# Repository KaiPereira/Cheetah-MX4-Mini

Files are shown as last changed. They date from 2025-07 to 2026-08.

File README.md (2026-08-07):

# Cheetah MX4 Mini Motherboard

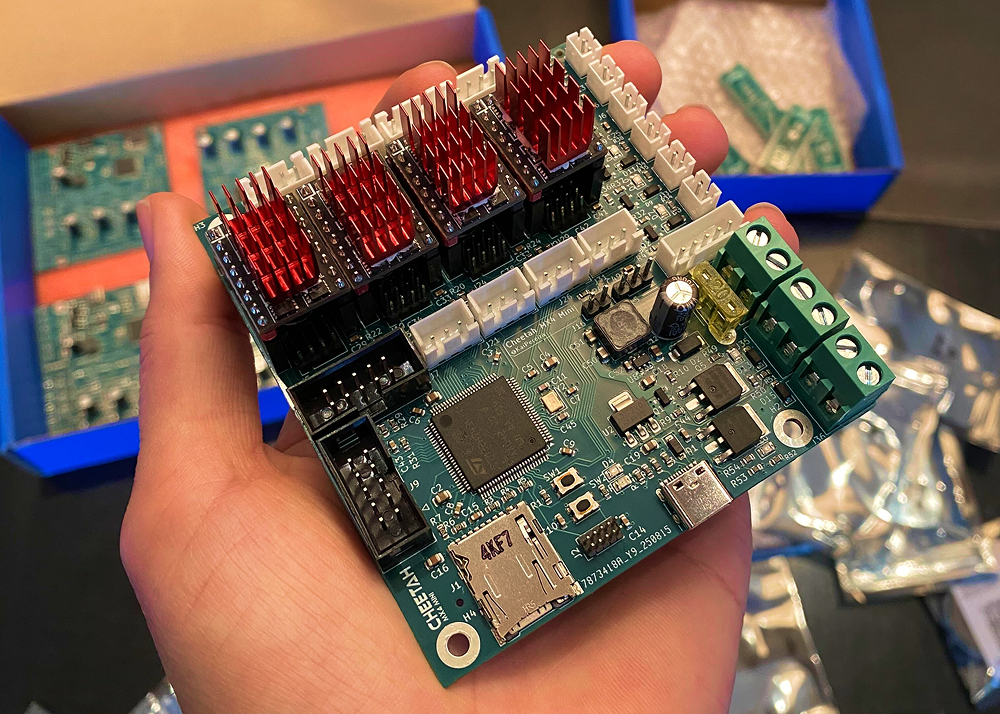
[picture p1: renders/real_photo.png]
PCB Photo


The Cheetah MX4 Mini is a fully open source, powerful, yet affordable 3D printer motherboard! At just 80x90mm wide, it's an extremely compact motherboard with many cool features! This is one of the first PCB's I've ever created, so it might have some flaws.
## Custom Features
- 4 TMC stepstick drivers that support UART and SPI
- Sensorless and endstop homing configured using jumpers
- 3 Thermistor input connectors
- Support for parallel and serial LCD's and TFT displays
- 3 Fan output connectors
- Support for the BLTouch Probe (servo and probe connectors too)
- 2 High amperage heater outputs for a bed and miscellaneous
- Powerful STM32H743VIT6 LQFP100 MCU
- Support for USB-C and SD-Card printing
- 4x M3 grounded mounting holes
- Status and Power LEDs for programming
- 12/24V, 15A Input

## PCB Design

The Cheetah MX4 Mini is a 4 layer PCB with dedicated power and ground inner layers. Don't mind the messy PCB/schematic, it was one of my first boards ;) 

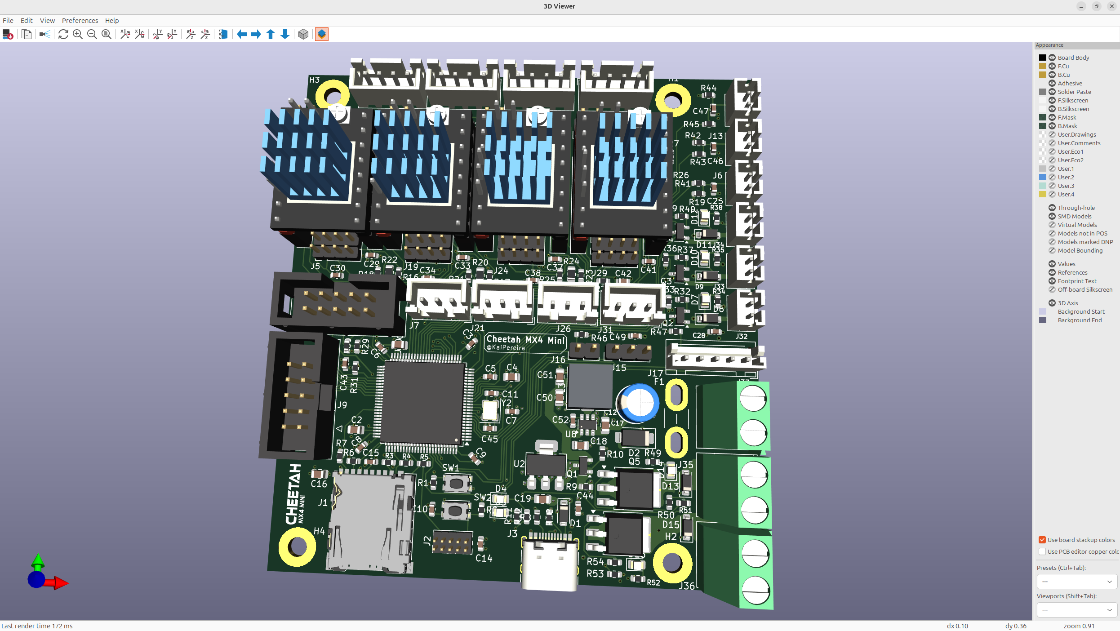
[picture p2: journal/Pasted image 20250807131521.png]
3D Model

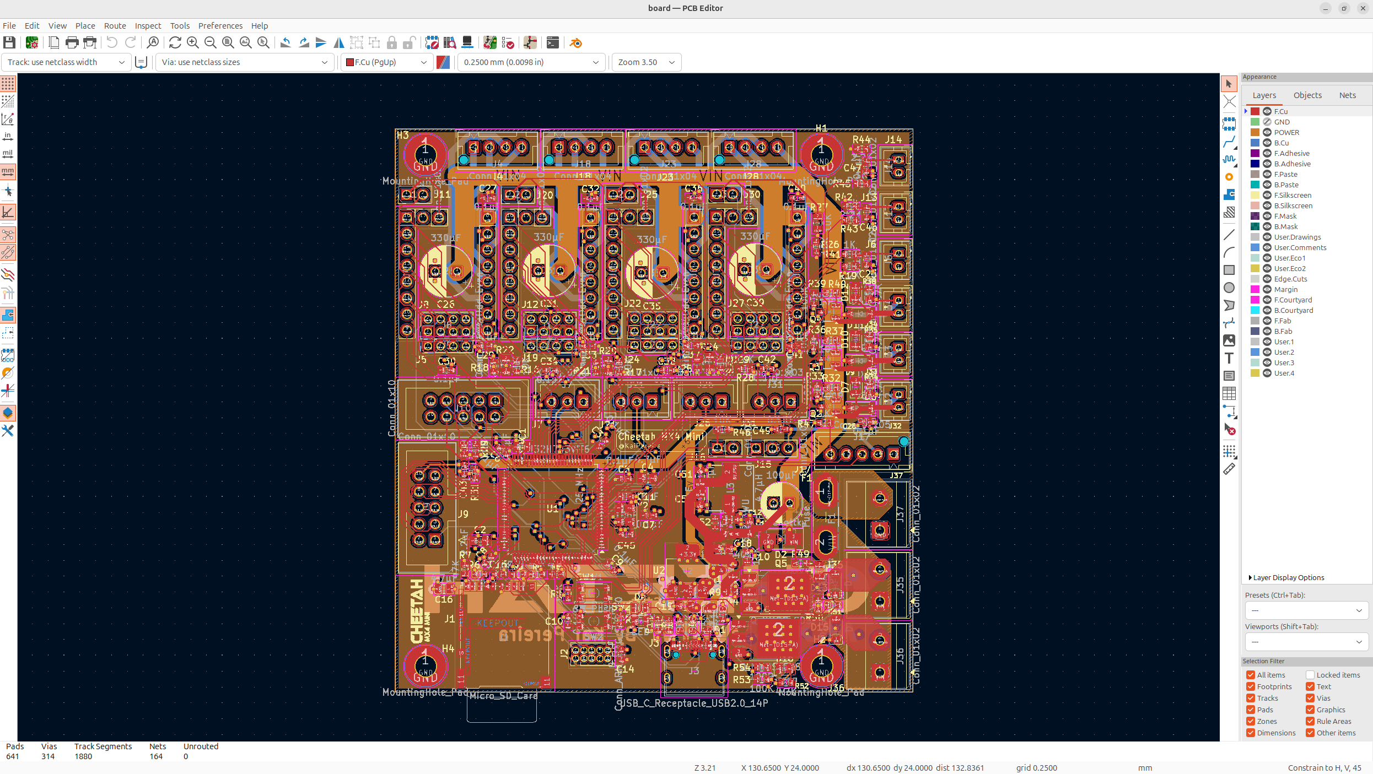
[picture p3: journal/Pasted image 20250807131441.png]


It's built off the STM32H series MCU to support every function you need for a printer. It's got many protection circuits, good decoupling, and is designed around high current inputs.

To power it, you can supply either USB-C for development, or a 12/24V PSU to drive the motors and all the other parts like the drivers.

You can upload prints via USB-C or SD Card, with support for UART and SPI TMC drivers, and you can hot-swap the motor drivers for maximum control.

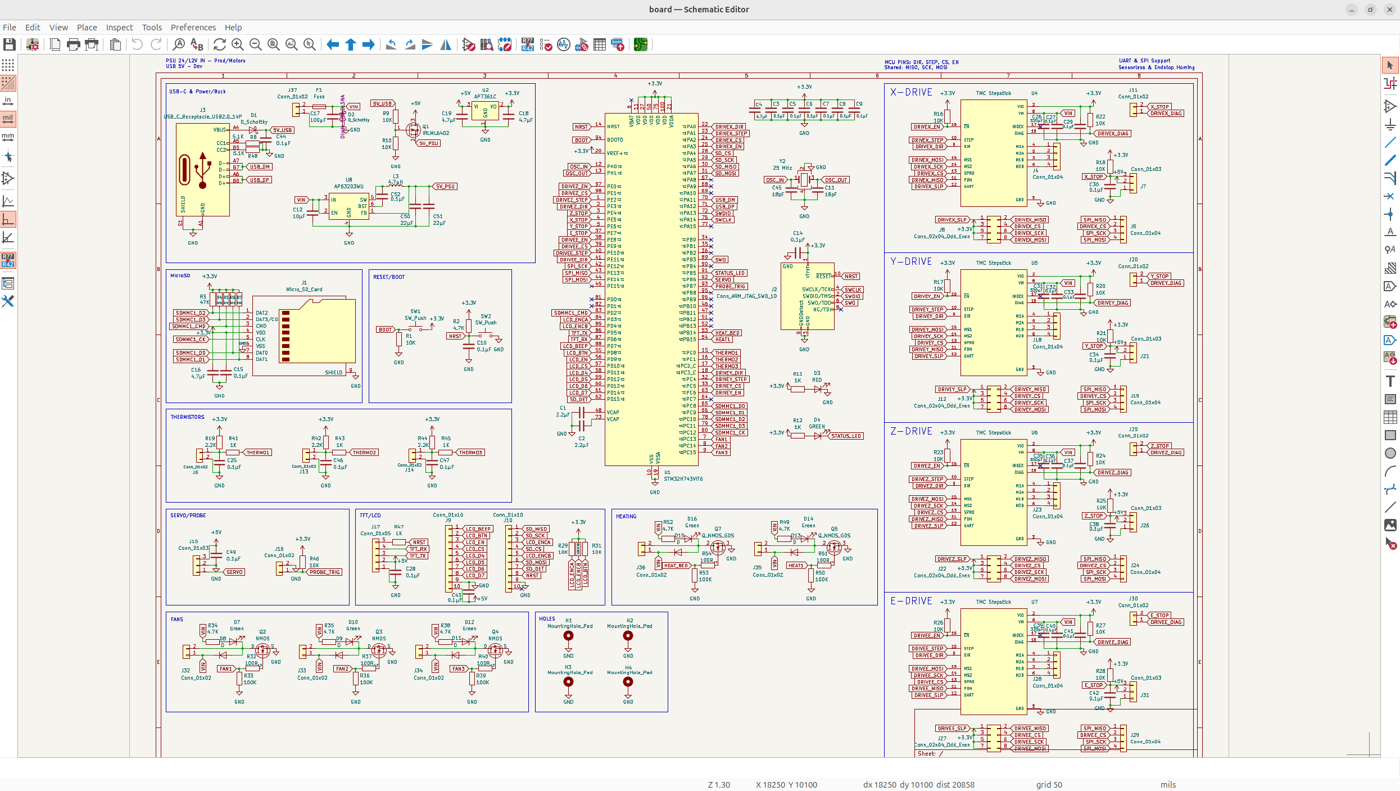
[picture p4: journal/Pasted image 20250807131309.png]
Schematic Photo

## Firmware

The Cheetah MX4 Mini uses an STM32H743VIT6 MCU, so it has support for both Marlin, Klipper and most other 3D printer firmwares!

To get started, you can upload firmware to the onboard flash using the dedicated boot and reset pins!

More information on firmware *coming soon...*

## BOM (Bill of Materials)

I've created a BOM for JLCPCB and a general footprint BOM if you want to get PCBA from somewhere else like PCBWay or something.

The JLCPCB BOM is actually relatively cheap, coming in at about $150 for all 5 boards which I was pretty impressed with!

The LCSC BOM costs about $20 for the actual parts and then shipping will be about $20.

You can find the JLCPCB BOM [here](/production/BOM_JLCPCB.csv).

The LCSC BOM [here](/production/BOM_LCSC.csv)

The general footprint BOM is [here](/production/BOM.csv).

There's also a pick and place formatted for [JLCPCB](/production/CPL_JLCPCB.csv) and a general one if you're using a different platform [here](/production/CPL.csv).

## Credits

Thanks so much to @Fisheiyy and for the folks on Reddit for reviewing and helping me with the board, without them, this board probably would have never worked or come to fruition! Thanks also to Hackclub, specifically @qcoral and @acornitum for running [Highway](https://highway.hackclub.com/) which sponsored the board!

## License
oshw_facts(1)

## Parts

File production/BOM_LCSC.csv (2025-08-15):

LCSC Part Number | Manufacture Part Number | Manufacturer | Customer NO. | Package | Description | RoHS | Quantity | Unit Price($) | Ext.Price($) | Estimated lead time (business days) | Date Code / Lot No. | Status
C161871 | B4B-XH-AM(LF)(SN) | JST |  | Through Hole,P=2.5mm | 1x4P 4P XH Tin 4 -25℃~+85℃ 3A 1 2.5mm Brass Through Hole Through Hole,P=2.5mm Wire To Board Connector ROHS | YES | 20 | 0.0784 | 1.57 |  |  | -
C161870 | B3B-XH-AM(LF)(SN) | JST |  | Through Hole,P=2.5mm | 1x3P 3P XH Tin 3 -25℃~+85℃ 3A 1 2.5mm Brass Through Hole Through Hole,P=2.5mm Wire To Board Connector ROHS | YES | 20 | 0.0546 | 1.09 |  |  | -
C161872 | B5B-XH-AM(LF)(SN) | JST |  | Through Hole,P=2.5mm | 1x5P 5P XH Tin 5 -25℃~+85℃ 3A 1 2.5mm Brass Through Hole Through Hole,P=2.5mm Wire To Board Connector ROHS | YES | 5 |  |  |  |  | Inquiring
C492401 | PZ254V-11-02P | XFCN |  | Through Hole,P=2.54mm | Through Hole Pin Header 2.5mm 2P 6mm -40℃~+105℃ 3mm 2.54mm 1 Black Brass 1x2P Through Hole,P=2.54mm Pin Headers ROHS | YES | 50 | 0.0135 | 0.68 |  |  | -
C2691448 | PZ254V-11-04P | XFCN |  | Through Hole,P=2.54mm | 250V 3A Through Hole Pin Header 2.5mm 4P 6mm -40℃~+105℃ 3mm 2.54mm 1 Black 1x4P Through Hole,P=2.54mm Pin Headers ROHS | YES | 60 | 0.0187 | 1.12 |  |  | -
C2937625 | PZ254V-11-03P | XFCN |  | Through Hole,P=2.54mm | 250V 3A Through Hole Pin Header 2.5mm 3P 6mm -40℃~+105℃ 3mm 2.54mm 1 Black 1x3P Through Hole,P=2.54mm Pin Headers ROHS | YES | 50 | 0.0141 | 0.71 |  |  | -
C131337 | B2B-PH-K-S(LF)(SN) | JST |  | Through Hole,P=2mm | 1x2P 2P PH Tin 2 -25℃~+85℃ 2A 1 2mm Brass Through Hole Through Hole,P=2mm Wire To Board Connector ROHS | YES | 40 | 0.0314 | 1.26 |  |  | -
C27438 | 2.54-1*8P | BOOMELE(Boom Precision Elec) |  | Through Hole,P=2.54mm | 2.54mm 1 8P Through Hole 1x8P Through Hole,P=2.54mm Female Headers ROHS | YES | 40 | 0.0768 | 3.07 |  |  | -
C49661 | 2.54-1*2P | BOOMELE(Boom Precision Elec) |  | Through Hole,P=2.54mm | 2.54mm 1 2P Through Hole 1x2P Through Hole,P=2.54mm Female Headers ROHS | YES | 20 | 0.0381 | 0.76 |  |  | -
C5665 | 2.54-2*5P | BOOMELE(Boom Precision Elec) |  | Through Hole,P=2.54mm | 2.54mm Through Hole 2x5P 5 IDC Header 2.54mm 2 Through Hole,P=2.54mm IDC Connectors ROHS | YES | 10 | 0.0745 | 0.75 |  |  | -
C18197869 | PZ127V-12-10-0720 | XFCN |  | Through Hole,P=1.27mm | Through Hole,P=1.27mm Pin Headers ROHS | YES | 10 | 0.0634 | 0.63 |  |  | -
C8465 | WJ500V-5.08-2P | KANGNEX |  | Through Hole,P=5.08mm | 1x2P 18A -40℃~+105℃ 250V Green 14~30 Through Hole 5.08mm 2.5 1 2 Through Hole,P=5.08mm Screw Terminal Blocks ROHS | YES | 15 | 0.1089 | 1.63 |  |  | -
C142685 | 0287020.PXCN | Littelfuse |  | - | 32V 1kA@32V Blade Fuse 20A Automotive Fuses ROHS | YES | 5 | 0.1009 | 0.50 |  |  | -
C142684 | 0287015.PXCN | Littelfuse |  | - | 32V 1kA@32V Blade Fuse 15A Automotive Fuses ROHS | YES | 5 | 0.1041 | 0.52 |  |  | -
C142683 | 0287010.PXCN | Littelfuse |  | - | 32V 1kA@32V Blade Fuse 10A Automotive Fuses ROHS | YES | 5 | 0.1001 | 0.50 |  |  | -

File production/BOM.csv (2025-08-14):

Id | Designator | Footprint | Quantity | Designation | Supplier and ref
1 | C51,C50 | C_0805_2012Metric | 2 | 22µF
2 | R33,R39,R36,R50,R53 | R_0603_1608Metric | 5 | 100K
3 | Q7,Q5 | TO-252-3_TabPin2 | 2 | Q_NMOS_GDS
4 | C45,C11 | C_0603_1608Metric | 2 | 18pF
5 | C15,C27,C7,C43,C40,C6,C32,C46,C28,C49,C8,C29,C3,C36,C10,C52,C37,C33,C30,C25,C38,C42,C34,C14,C9,C41,C47,C44,C5 | C_0603_1608Metric | 29 | 0.1µF
6 | R10,R26,R25,R18,R21,R16,R1,R30,R28,R29,R31,R46,R9,R17,R23 | R_0603_1608Metric | 15 | 10K
7 | J2 | PinHeader_2x05_P1.27mm_Vertical | 1 | Conn_ARM_JTAG_SWD_10
8 | J19,J29,J24,J5 | PinHeader_1x04_P2.00mm_Vertical | 4 | Conn_01x04
9 | J12,J27,J22,J8 | PinHeader_2x04_P2.00mm_Vertical | 4 | Conn_02x04_Odd_Even
10 | C19,C18,C16,C4 | C_0805_2012Metric | 4 | 4.7µF
11 | J4,J28,J18,J23 | JST_XH_B4B-XH-AM_1x04_P2.50mm_Vertical | 4 | Conn_01x04
12 | SW2,SW1 | SW_Push_1P1T_NO_CK_KMR2 | 2 | SW_Push
13 | R12,R11,R47,R45,R43,R41 | R_0603_1608Metric | 6 | 1K
14 | R49,R2,R34,R35,R38,R52 | R_0603_1608Metric | 6 | 4.7K
15 | L3 | L_Wuerth_HCM-7070 | 1 | 4.7µH
16 | J11,J30,J20,J16,J25 | PinHeader_1x02_P2.54mm_Vertical | 5 | Conn_01x02
17 | D10,D7,D4,D16,D12,D14 | LED_0805_2012Metric | 6 | Green
18 | R40,R51,R37,R32,R54 | R_0603_1608Metric | 5 | 100R
19 | U2 | SOT-223-3_TabPin2 | 1 | AP7361C
20 | U5,U7,U4,U6 | TMC Stepstick | 4 | TMC Stepstick
21 | D1 | D_SOD-123 | 1 | D_Schottky
22 | R20,R27,R22,R24 | R_0805_2012Metric | 4 | 10K
23 | J13,J14,J33,J6,J34,J32 | JST_PH_B2B-PH-K_1x02_P2.00mm_Vertical | 6 | Conn_01x02
24 | U1 | LQFP-100_14x14mm_P0.5mm | 1 | STM32H743VIT6
25 | R7,R3,R4,R6,R5 | R_0603_1608Metric | 5 | 47K
26 | Q3,Q4,Q2 | SOT-23-3 | 3 | NMOS
27 | U8 | TSOT-23-6 | 1 | AP63203WU
28 | J36,J37,J35 | TerminalBlock_Phoenix_MKDS-1,5-2-5.08_1x02_P5.08mm_Horizontal | 3 | Conn_01x02
29 | D2 | D_SMA | 1 | D_Schottky
30 | C39,C31,C35,C26 | CP_Radial_D8.0mm_P3.50mm | 4 | 330µF
31 | D13,D15,D9,D8,D11 | D_SOD-123 | 5 | D
32 | J26,J7,J31,J21 | JST_XH_B3B-XH-A_1x03_P2.50mm_Vertical | 4 | Conn_01x03
33 | J17 | JST_XH_B5B-XH-AM_1x05_P2.50mm_Vertical | 1 | Conn_01x05
34 | R48,R8 | R_0603_1608Metric | 2 | 5.1K
35 | F1 | Fuse_Blade_Mini_directSolder | 1 | Fuse
36 | J1 | microSD_HC_Hirose_DM3AT-SF-PEJM5 | 1 | Micro_SD_Card
37 | R44,R42,R19 | R_0603_1608Metric | 3 | 2.2K
38 | J15 | PinHeader_1x03_P2.54mm_Vertical | 1 | Conn_01x03
39 | J3 | USB_C_Receptacle_HRO_TYPE-C-31-M-12 | 1 | USB_C_Receptacle_USB2.0_14P
40 | D3 | LED_0805_2012Metric | 1 | RED
41 | C12 | C_0805_2012Metric | 1 | 10µF
42 | J9,J10 | IDC-Header_2x05_P2.54mm_Vertical | 2 | Conn_01x10
43 | C17 | CP_Radial_D6.3mm_P2.50mm | 1 | 100µF
44 | C2,C1 | C_0805_2012Metric | 2 | 2.2µF
45 | Y2 | Crystal_SMD_3225-4Pin_3.2x2.5mm | 1 | 25 MHz
46 | Q1 | SOT-23 | 1 | IRLML6402

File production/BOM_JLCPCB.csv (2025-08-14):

JLCPCB BOM Tool - BOM Matching
BOM name：BOM-JLCPCB Assembly Order.xlsx |  |  | Download Time：2025-08-11 07:53:41 |  |  |  | * Our matching results are updated in real-time, but stock and prices may change. If it's been over 24 hours, please re-match before placing your order.
PCB Assembled Qty：5 |  |  | Est. Total Price：65.4786
Your BOM |  |  |  |  | Matched Parts |  |  |  |  |  |  | Order Information
Top Designator | Bottom Designator | Comment | Footprint | JLCPCB Part # | Matches | Part # | Manufacturer | Footprint | Description | Category | Warning | JLCPCB Part # | Product link | Lib Type | Qty | Source | Total Price ($)
C1,C2 |  | 2.2碌F | 0805 |  | Select by System | CL21A225KBQNNNE | Samsung Electro-Mechanics | 0805 | 2.2uF 50V X5R ±10% 0805 Multilayer Ceramic Capacitors MLCC - SMD/SMT ROHS | Multilayer Ceramic Capacitors MLCC - SMD/SMT |  | C377773 | https://jlcpcb.com/partdetail/350246-CL21A225KBQNNNE/C377773 | Basic | 10 | 10 JLCPCB | 0.145
C3,C5,C6,C7,C8,C9,C10,C14,C15,C25,C27,C28,C29,C30,C32,C33,C34,C36,C37,C38,C40,C41,C42,C43,C44,C46,C47,C49,C52 |  | 0.1碌F | 0603 |  | Select by System | CC0603KRX7R9BB104 | YAGEO | 0603 | 100nF 50V X7R ±10% 0603 Multilayer Ceramic Capacitors MLCC - SMD/SMT ROHS | Multilayer Ceramic Capacitors MLCC - SMD/SMT |  | C14663 | https://jlcpcb.com/partdetail/YAGEO-CC0603KRX7R9BB104/C14663 | Basic | 145 | 145 JLCPCB | 0.3335
C4,C16,C18,C19 |  | 4.7碌F | 0805 |  | Select by System | CL21A475KAQNNNE | Samsung Electro-Mechanics | 0805 | 25V 4.7uF X5R ±10% 0805 Multilayer Ceramic Capacitors MLCC - SMD/SMT ROHS | Multilayer Ceramic Capacitors MLCC - SMD/SMT |  | C1779 | https://jlcpcb.com/partdetail/2131-CL21A475KAQNNNE/C1779 | Basic | 20 | 20 JLCPCB | 0.25
C11,C45 |  | 18pF | 0603 |  | Select by System | CL10C180JB8NNNC | Samsung Electro-Mechanics | 0603 | 18pF 50V C0G ±5% 0603 Multilayer Ceramic Capacitors MLCC - SMD/SMT ROHS | Multilayer Ceramic Capacitors MLCC - SMD/SMT |  | C1647 | https://jlcpcb.com/partdetail/1999-CL10C180JB8NNNC/C1647 | Basic | 10 | 10 JLCPCB | 0.051
C12 |  | 10碌F | 0805 |  | Select by System | CL21A106KAYNNNE | Samsung Electro-Mechanics | 0805 | 10uF 25V X5R ±10% 0805 Multilayer Ceramic Capacitors MLCC - SMD/SMT ROHS | Multilayer Ceramic Capacitors MLCC - SMD/SMT |  | C15850 | https://jlcpcb.com/partdetail/16532-CL21A106KAYNNNE/C15850 | Basic | 5 | 5 JLCPCB | 0.054
C17 |  | 100碌F | 插件,D6.3xL11mm |  | Select by System | NXA25V100M6.3*11 2.5TP | SamYoung Electronics | 插件,D6.3xL11mm | -40℃~+105℃ 100uF 11mm 2.5mm 220mΩ@100kHz 25V 340mA@100kHz 5000hrs@105℃ 6.3mm ±20% Plugin,D6.3xL11mm Aluminum Electrolytic Capacitors - Leaded ROHS | Aluminum Electrolytic Capacitors - Leaded |  | C165558 | https://jlcpcb.com/partdetail/176941-NXA25V100M6_3_11_25TP/C165558 | Extended | 6 | 6 JLCPCB | 0.4962
C26,C31,C35,C39 |  | 330碌F | 插件,D8xL12mm |  | Select by System | KM337M025F12RR0VH2FP0 | CX(Dongguan Chengxing Elec) | 插件,D8xL12mm | 12mm 2000hrs@105℃ 25V 3.5mm 330uF 340mA@120Hz 8mm ±20% Plugin,D8xL12mm Aluminum Electrolytic Capacitors - Leaded ROHS | Aluminum Electrolytic Capacitors - Leaded |  | C2051 | https://jlcpcb.com/partdetail/2403-KM337M025F12RR0VH2FP0/C2051 | Extended | 21 | 21 JLCPCB | 0.819
C50,C51 |  | 22碌F | 0805 |  | Select by System | CL21A226MAQNNNE | Samsung Electro-Mechanics | 0805 | 22uF 25V X5R ±20% 0805 Multilayer Ceramic Capacitors MLCC - SMD/SMT ROHS | Multilayer Ceramic Capacitors MLCC - SMD/SMT |  | C45783 | https://jlcpcb.com/partdetail/46786-CL21A226MAQNNNE/C45783 | Basic | 10 | 10 JLCPCB | 0.237
D1 |  | D_Schottky | SOD-123 |  | Select by System | B0530W | Jiangsu Changjing Electronics Technology Co., Ltd. | SOD-123 | 30V 430mV@500mA SOD-123 Schottky Diodes ROHS | Schottky Diodes |  | C2102 | https://jlcpcb.com/partdetail/2459-B0530W/C2102 | Extended | 9 | 9 JLCPCB | 0.3159
D2 |  | D_Schottky | SMA(DO-214AC) |  | Select by System | SS54 | MDD(Microdiode Semiconductor) | SMA(DO-214AC) | 1mA@40V 40V 550mV@5A 5A Independent SMA(DO-214AC) Schottky Diodes ROHS | Schottky Diodes |  | C22452 | https://jlcpcb.com/partdetail/MDD_Microdiode_Semiconductor-SS54/C22452 | Basic | 5 | 5 JLCPCB | 0.2125
D3 |  | RED | 0805 |  | Select by System | NCD0805R1 | Foshan NationStar Optoelectronics | 0805 | -30℃~+85℃ 1.6V~2.6V 130° 25mA 615nm~630nm 65mW 67mcd~195mcd Discrete Diode Red 0805 LED Indication - Discrete ROHS | LED Indication - Discrete |  | C84256 | https://jlcpcb.com/partdetail/85425-NCD0805R1/C84256 | Basic | 5 | 5 JLCPCB | 0.066
D4 |  | GREEN | 0805 |  | Select by System | KT-0805G | Hubei KENTO Elec | 0805 | Emerald Green 0805 LED Indication - Discrete ROHS | LED Indication - Discrete | 1.Multiple lines in the BOM have been matched to the same part. Please check if the matching is correct. ; | C2297 | https://jlcpcb.com/partdetail/Hubei_KENTOElec-KT0805G/C2297 | Basic | 30 | 30 JLCPCB | 0.321
D7,D10,D12,D14,D16 |  | Green | 0805 |  | Select by System
D8,D9,D11,D13,D15 |  | D | SOD-123 |  | Select by System | B5819W SL | Jiangsu Changjing Electronics Technology Co., Ltd. | SOD-123 | 1A 40V 600mV@1A 9A SOD-123 Schottky Diodes ROHS | Schottky Diodes |  | C8598 | https://jlcpcb.com/partdetail/9093-B5819WSL/C8598 | Basic | 25 | 25 JLCPCB | 0.545
J1 |  | Micro_SD_Card | SMD |  | Select by System | DM3AT-SF-PEJM5 | HRS(Hirose) | SMD | -25℃~+85℃ 1.68mm Connector and Ejector MicroSD Card (TF Card) No Push-Push SMD SD Card / Memory Card Connector ROHS | SD Card / Memory Card Connector |  | C114218 | https://jlcpcb.com/partdetail/HRS_Hirose-DM3AT_SFPEJM5/C114218 | Extended | 5 | 5 JLCPCB | 6.45
J2 |  | Conn_ARM_JTAG_SWD_10 | 插件,P=1.27mm |  | Select by System | PH-00555 | Liansheng | 插件,P=1.27mm | -40℃~+105℃ 1.27mm 1.27mm 10P 1A 2 2.5mm 2x5P 3mm 4mm Black Pin Header Through Hole Plugin,P=1.27mm Pin Headers ROHS | Pin Headers |  | C2685167 | https://jlcpcb.com/partdetail/Liansheng-PH00555/C2685167 | Extended | 0 | 0 JLCPCB | 0
J3 |  | USB_C_Receptacle_USB2.0_14P | SMD |  | Select by System | TYPE-C-31-M-12 | Korean Hroparts Elec | SMD | 1 16P 5A Female Type-C SMD USB Connectors ROHS | USB Connectors |  | C165948 | https://jlcpcb.com/partdetail/Korean_HropartsElec-TYPE_C_31_M12/C165948 | Extended | 5 | 5 JLCPCB | 0.8485
J4,J18,J23,J28 |  | Conn_01x04 | 插件,P=2.5mm |  | Select by System | B4B-XH-AM(LF)(SN) | JST | 插件,P=2.5mm | -25℃~+85℃ 1 12.4mm 1x4P 2.5mm 250V 3A 4 4P 5.75mm 7mm Brass K Pin PA66 Through Hole Tin UL94V-0 White XH Plugin,P=2.5mm Wire To Board Connector ROHS | Wire To Board Connector |  | C161871 | https://jlcpcb.com/partdetail/JST-B4B_XH_AM_LF_SN/C161871 | Extended | 0 | 0 JLCPCB | 0
J5,J19,J24,J29 |  | Conn_01x04 | 插件,P=2mm |  | Select by System | KH-2PH180-1X4P-L8.7 | Shenzhen Kinghelm Elec | 插件,P=2mm | -40℃~+105℃ 1 1.5A 1x4P 2.8mm 2mm 2mm 3.9mm 4P Pin Header Through Hole Plugin,P=2mm Pin Headers ROHS | Pin Headers |  | C2938451 | https://jlcpcb.com/partdetail/3294831-KH_2PH180_1X4P_L87/C2938451 | Extended | 0 | 0 JLCPCB | 0
J6,J13,J14,J32,J33,J34 |  | Conn_01x02 | 插件,P=2mm |  | Select by System | B2B-PH-K-S(LF)(SN) | JST | 插件,P=2mm | -25℃~+85℃ 1 100V 1x2P 2 2A 2P 2mm 4.5mm 5.9mm 6mm Brass K Pin PA66 PH Through Hole Tin UL94V-0 White Plugin,P=2mm Wire To Board Connector ROHS | Wire To Board Connector |  | C131337 | https://jlcpcb.com/partdetail/JST-B2B_PH_K_S_LF_SN/C131337 | Extended | 0 | 0 JLCPCB | 0
J7,J21,J26,J31 |  | Conn_01x03 | 插件,P=2.5mm |  | Select by System | B3B-XH-AM(LF)(SN) | JST | 插件,P=2.5mm | -25℃~+85℃ 1 1x3P 2.5mm 250V 3 3A 3P 5.75mm 7mm 9.9mm Brass K Pin PA66 Through Hole Tin UL94V-0 White XH Plugin,P=2.5mm Wire To Board Connector ROHS | Wire To Board Connector |  | C161870 | https://jlcpcb.com/partdetail/JST-B3B_XH_AM_LF_SN/C161870 | Extended | 0 | 0 JLCPCB | 0
J8,J12,J22,J27 |  | Conn_02x04_Odd_Even | 插件,P=2mm |  | Select by System | A2005WV-2x4P | CJT(Changjiang Connectors) | 插件,P=2mm | -40℃~+105℃ 2 2.8mm 2mm 2mm 2x4P 4mm 8P Black Brass Pin Header Through Hole Plugin,P=2mm Pin Headers ROHS | Pin Headers |  | C225289 | https://jlcpcb.com/partdetail/225572-A2005WV2x4P/C225289 | Extended | 0 | 0 JLCPCB | 0
J9,J10 |  | Conn_01x10 | 插件,P=2.54mm |  | Select by System | 2.54-2*5P简牛 | BOOMELE(Boom Precision Elec) | 插件,P=2.54mm | 2 2.54mm 2.54mm 2x5P 5 IDC Header Through Hole Plugin,P=2.54mm IDC Connectors ROHS | IDC Connectors |  | C5665 | https://jlcpcb.com/partdetail/BOOMELE_Boom_Precision_Elec-2_54_2_5P/C5665 | Extended | 0 | 0 JLCPCB | 0
J11,J16,J20,J25,J30 |  | Conn_01x02 | 插件,P=2.54mm |  | Select by System | HX PZ2.54-1x2P ZZ | hanxia | 插件,P=2.54mm | -40℃~+105℃ 1 1x2P 2.54mm 2.5mm 2P 3A 3mm 6mm Black Brass Gold Pin Header Through Hole Plugin,P=2.54mm Pin Headers ROHS | Pin Headers |  | C32713268 | https://jlcpcb.com/partdetail/hanxia-HX_PZ2_54_1x2PZZ/C32713268 | Extended | 0 | 0 JLCPCB | 0
J15 |  | Conn_01x03 | 插件,P=2.54mm |  | Select by System | 2.54-1*3P针 | BOOMELE(Boom Precision Elec) | 插件,P=2.54mm | -40℃~+105℃ 1 1x3P 2.54mm 3A 3P Black Pin Header Through Hole Plugin,P=2.54mm Pin Headers ROHS | Pin Headers |  | C49257 | https://jlcpcb.com/partdetail/50265-2_54_1_3P/C49257 | Extended | 0 | 0 JLCPCB | 0
J17 |  | Conn_01x05 | 插件,P=2.5mm |  | Select by System | B5B-XH-A(LF)(SN) | JST | 插件,P=2.5mm | -25℃~+85℃ 1 14.9mm 1x5P 2.5mm 250V 3A 5 5.75mm 5P 7mm Brass K Pin PA66 Through Hole Tin UL94V-0 White XH Plugin,P=2.5mm Wire To Board Connector ROHS | Wire To Board Connector |  | C157991 | https://jlcpcb.com/partdetail/JST-B5B_XH_A_LF_SN/C157991 | Extended | 0 | 0 JLCPCB | 0
J35,J36,J37 |  | Conn_01x02 | 插件,P=5mm |  | Select by System | DG128-5.0-02P-14-00A(H) | DEGSON | 插件,P=5mm | -40℃~+105℃ 1 12~30 1x2P 2 2.5 20A 2P 300V 5mm Green Through Hole Plugin,P=5mm Screw Terminal Blocks ROHS | Screw Terminal Blocks |  | C711349 | https://jlcpcb.com/partdetail/DEGSON-DG128_5_0_02P_14_00A_H/C711349 | Extended | 0 | 0 JLCPCB | 0
L3 |  | 4.7碌H | 1212 |  | Select by System | 74438334047 | Wurth Elektronik | 1212 | 1.1A 3.8A 307.8mΩ 4.7uH AEC-Q200 ±20% 1212 Power Inductors ROHS | Power Inductors |  | C5542263 | https://jlcpcb.com/partdetail/WurthElektronik-74438334047/C5542263 | Extended | 5 | 5 JLCPCB | 7.155
Q1 |  | IRLML6402 | SOT-23 |  | Select by System | IRLML6402 | BORN | SOT-23 | -55℃~+150℃ 1 P-Channel 1.1W 1.2V 20V 3.7A 600pF 80mΩ@2.5V,3.1A SOT-23 MOSFETs ROHS | MOSFETs |  | C5148470 | https://jlcpcb.com/partdetail/BORN-IRLML6402/C5148470 | Extended | 9 | 9 JLCPCB | 0.4635
Q2,Q3,Q4 |  | NMOS | SOT-23 |  | Select by System | IRLML6344 | Guangdong Hottech | SOT-23 | -55℃~+150℃ 1 N-Channel 1.1V 1.3W 29mΩ@4.5V,5A 30V 46pF@15V 5A 6.8nC@4.5V 650pF@25V SOT-23 MOSFETs ROHS | MOSFETs |  | C5364313 | https://jlcpcb.com/partdetail/GuangdongHottech-IRLML6344/C5364313 | Extended | 19 | 19 JLCPCB | 0.798
Q5,Q7 |  | Q_NMOS_GDS | TO-252(D2PAK) |  | No matches |  |  |  |  | MOSFETs |  | C19188232 | https://jlcpcb.com/partdetail/VBsemiElec-IRLZ44NSPBFVB/C19188232 | Extended | 10 | 10 JLCPCB | 5.955
R1,R9,R10,R16,R17,R18,R21,R23,R25,R26,R28,R29,R30,R31,R46 |  | 10K | 0603 |  | Select by System | 0603WAF1002T5E | UNI-ROYAL(Uniroyal Elec) | 0603 | -55℃~+155℃ 100mW 10kΩ 75V Thick Film Resistor ±1% ±100ppm/℃ 0603 Chip Resistor - Surface Mount ROHS | Chip Resistor - Surface Mount |  | C25804 | https://jlcpcb.com/partdetail/26547-0603WAF1002T5E/C25804 | Basic | 75 | 75 JLCPCB | 0.0675
R2,R34,R35,R38,R49,R52 |  | 4.7K | 0603 |  | Select by System | 0603WAF4701T5E | UNI-ROYAL(Uniroyal Elec) | 0603 | -55℃~+155℃ 100mW 4.7kΩ 75V Thick Film Resistor ±1% ±100ppm/℃ 0603 Chip Resistor - Surface Mount ROHS | Chip Resistor - Surface Mount |  | C23162 | https://jlcpcb.com/partdetail/23889-0603WAF4701T5E/C23162 | Basic | 30 | 30 JLCPCB | 0.033
R3,R4,R5,R6,R7 |  | 47K | 0603 |  | Select by System | 0603WAF4702T5E | UNI-ROYAL(Uniroyal Elec) | 0603 | -55℃~+155℃ 100mW 47kΩ 75V Thick Film Resistor ±1% ±100ppm/℃ 0603 Chip Resistor - Surface Mount ROHS | Chip Resistor - Surface Mount |  | C25819 | https://jlcpcb.com/partdetail/26562-0603WAF4702T5E/C25819 | Basic | 25 | 25 JLCPCB | 0.0275
R8,R48 |  | 5.1K | 0603 |  | Select by System | 0603WAF5101T5E | UNI-ROYAL(Uniroyal Elec) | 0603 | -55℃~+155℃ 100mW 5.1kΩ 75V Thick Film Resistor ±1% ±100ppm/℃ 0603 Chip Resistor - Surface Mount ROHS | Chip Resistor - Surface Mount |  | C23186 | https://jlcpcb.com/partdetail/23913-0603WAF5101T5E/C23186 | Basic | 10 | 10 JLCPCB | 0.01
R11,R12,R41,R43,R45,R47 |  | 1K | 0603 |  | Select by System | 0603WAF1001T5E | UNI-ROYAL(Uniroyal Elec) | 0603 | -55℃~+155℃ 100mW 1kΩ 75V Thick Film Resistor ±1% ±100ppm/℃ 0603 Chip Resistor - Surface Mount ROHS | Chip Resistor - Surface Mount |  | C21190 | https://jlcpcb.com/partdetail/21904-0603WAF1001T5E/C21190 | Basic | 30 | 30 JLCPCB | 0.03
R19,R42,R44 |  | 2.2K | 0603 |  | Select by System | 0603WAF2201T5E | UNI-ROYAL(Uniroyal Elec) | 0603 | -55℃~+155℃ 100mW 2.2kΩ 75V Thick Film Resistor ±1% ±100ppm/℃ 0603 Chip Resistor - Surface Mount ROHS | Chip Resistor - Surface Mount |  | C4190 | https://jlcpcb.com/partdetail/4597-0603WAF2201T5E/C4190 | Basic | 15 | 15 JLCPCB | 0.015
R20,R22,R24,R27 |  | 10K | 0805 |  | Select by System | 0805W8F1002T5E | UNI-ROYAL(Uniroyal Elec) | 0805 | -55℃~+155℃ 10kΩ 125mW 150V Thick Film Resistor ±1% ±100ppm/℃ 0805 Chip Resistor - Surface Mount ROHS | Chip Resistor - Surface Mount |  | C17414 | https://jlcpcb.com/partdetail/18102-0805W8F1002T5E/C17414 | Basic | 20 | 20 JLCPCB | 0.034
R32,R37,R40,R51,R54 |  | 100R | 0603 |  | Select by System | 0603WAF1000T5E | UNI-ROYAL(Uniroyal Elec) | 0603 | -55℃~+155℃ 100mW 100Ω 75V Thick Film Resistor ±1% ±100ppm/℃ 0603 Chip Resistor - Surface Mount ROHS | Chip Resistor - Surface Mount |  | C22775 | https://jlcpcb.com/partdetail/23502-0603WAF1000T5E/C22775 | Basic | 25 | 25 JLCPCB | 0.025
R33,R36,R39,R50,R53 |  | 100K | 0603 |  | Select by System | 0603WAF1003T5E | UNI-ROYAL(Uniroyal Elec) | 0603 | -55℃~+155℃ 100kΩ 100mW 75V Thick Film Resistor ±1% ±100ppm/℃ 0603 Chip Resistor - Surface Mount ROHS | Chip Resistor - Surface Mount |  | C25803 | https://jlcpcb.com/partdetail/26546-0603WAF1003T5E/C25803 | Basic | 25 | 25 JLCPCB | 0.025
SW1,SW2 |  | SW_Push | SMD |  | Select by System | KMR221GLFS | C&K | SMD | -40℃~+85℃ 1.9mm 2.8mm 2N 32V 4.6mm 50mA Gull Wing Round Button SPST Surface Mount,Vertical SMD Tactile Switches ROHS | Tactile Switches |  | C72443 | https://jlcpcb.com/partdetail/CK-KMR221GLFS/C72443 | Extended | 10 | 10 JLCPCB | 4.89
U1 |  | STM32H743VIT6 | LQFP-100(14x14) |  | Select by System | STM32H743VIT6 | STMicroelectronics | LQFP-100(14x14) | 1.71V~3.6V 12bit 16bit 2MB 480MHz 82 ARM Cortex-M Series LQFP-100(14x14) Microcontrollers (MCU/MPU/SOC) ROHS | Microcontrollers (MCU/MPU/SOC) |  | C114409 | https://jlcpcb.com/partdetail/STMicroelectronics-STM32H743VIT6/C114409 | Extended | 5 | 5 JLCPCB | 31.635
U2 |  | AP7361C | SOT-223R |  | Select by System | AP7361C-25ER-13 | Diodes Incorporated | SOT-223R | -40℃~+85℃@(Ta) 1 1A 2.5V 250mV@(1A) 60uA 6V 75dB@(1kHz) Fixed Over Current Protection Positive SOT-223R Voltage Regulators - Linear, Low Drop Out (LDO) Regulators ROHS | Voltage Regulators - Linear, Low Drop Out (LDO) Regulators |  | C460396 | https://jlcpcb.com/partdetail/DiodesIncorporated-AP7361C_25ER13/C460396 | Extended | 5 | 5 JLCPCB | 0.736
U8 |  | AP63203WU | TSOT-23-6 |  | Select by System | AP63203WU-7 | Diodes Incorporated | TSOT-23-6 | -40℃~+85℃@(TA) 1 1.1MHz 22uA 2A 3.3V 3.8V~32V Buck Buck Built-in Fixed Yes TSOT-23-6 DC-DC Converters ROHS | DC-DC Converters |  | C780769 | https://jlcpcb.com/partdetail/DiodesIncorporated-AP63203WU7/C780769 | Extended | 5 | 5 JLCPCB | 1.7925
Y2 |  | 25MHz | SMD3225-4P |  | Select by System | X322525MOB4SI | YXC Crystal Oscillators | SMD3225-4P | -40℃~+85℃ 12pF 25MHz Crystal Oscillator ±10ppm ±20ppm SMD3225-4P Crystals ROHS | Crystals |  | C9006 | https://jlcpcb.com/partdetail/YXC_CrystalOscillators-X322525MOB4SI/C9006 | Basic | 5 | 5 JLCPCB | 0.321
F1 |  | Fuse |  |  | No matches | No Part Selected
U4,U5,U6,U7 |  | TMCStepstick |  |  | No matches | No Part Selected

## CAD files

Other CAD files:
renders/render.blend

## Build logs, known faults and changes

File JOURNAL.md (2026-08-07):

---
title: Cheetah MX4 Mini
author: Kai Pereira
description: A powerful yet compact 3D printer motherboard that supports TMC stepsticks, fans, heaters, screens and thermistors 
created_at: 2025-07-20
---
### Total time spent: 86 Hours

## Day 1 - Getting started! - July 20th - 6 Hours

I've decided to build a complex 3D printer driver board, similar to the Manta M4P or the SKR Mini E3, but with some added features I have yet to decide.

I'm not too good at PCB work, I've only designed like keyboards and macropads and such, so I'm excited for a way harder PCB project!

The problem is, I have just about 10 days to complete this entire or I won't get the grant! So let's get right into building it.

The first thing I had to decide on was the MCU. I decided on using the STM32H743, it's an insanely powerful MCU that has many features I love:
- 2 MB Flash, 1 MB Ram (for firmware and G-Code Interpreter and stuff)
- Ethernet MAC (so I can network the printer)
- 480 MHz Processor
- Support for every communication protocol imaginable
- Good firmware support
- Blazingly fast and powerful

So let's just add in the MCU:

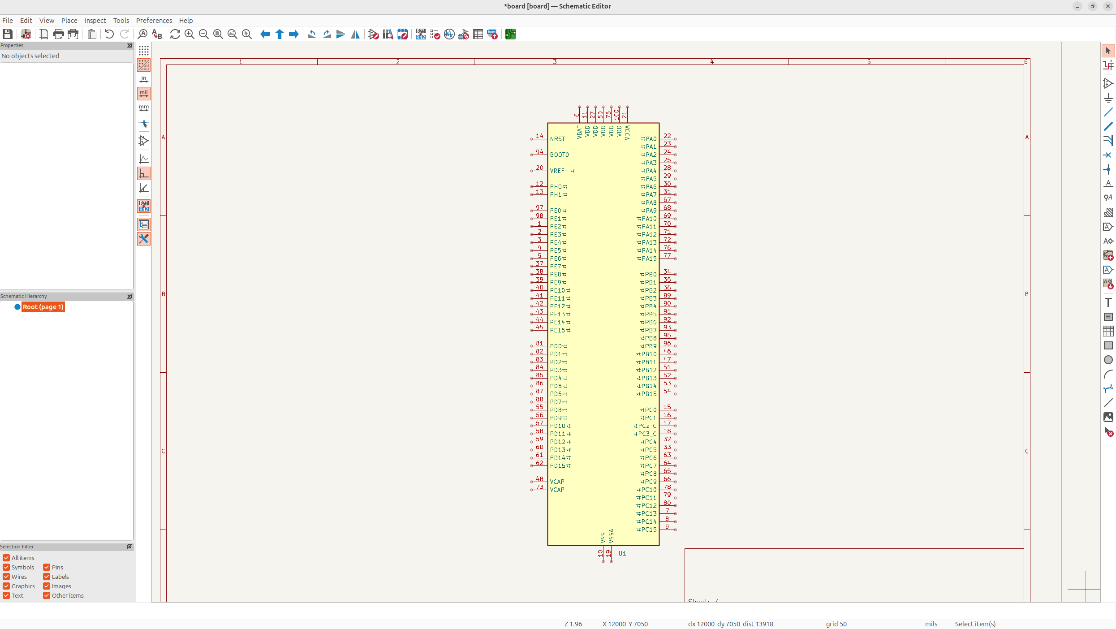
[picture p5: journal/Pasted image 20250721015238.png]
Pasted image 20250721015238.png

Then of course, I'm going to connect all the simple pins like VDD and GND:

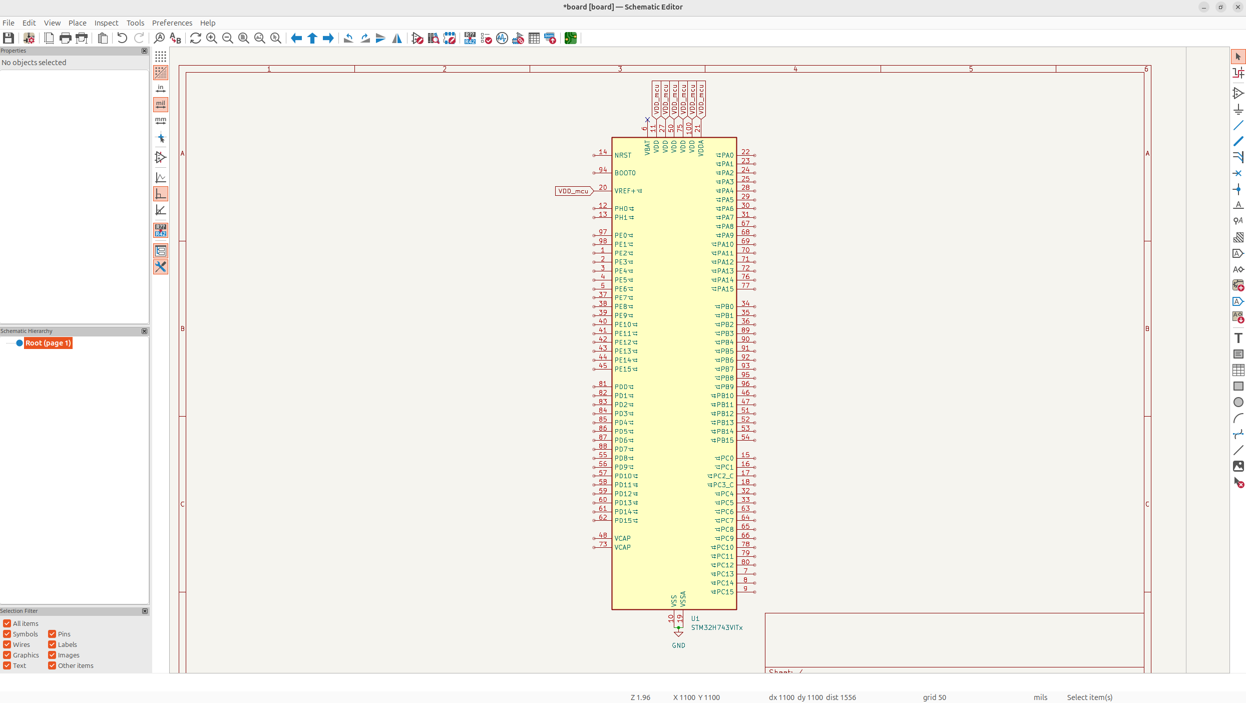
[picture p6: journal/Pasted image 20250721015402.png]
Pasted image 20250721015402.png

Next, each VDD needs a decoupling capacitor, and then a larger one for VDDA and VSSA:

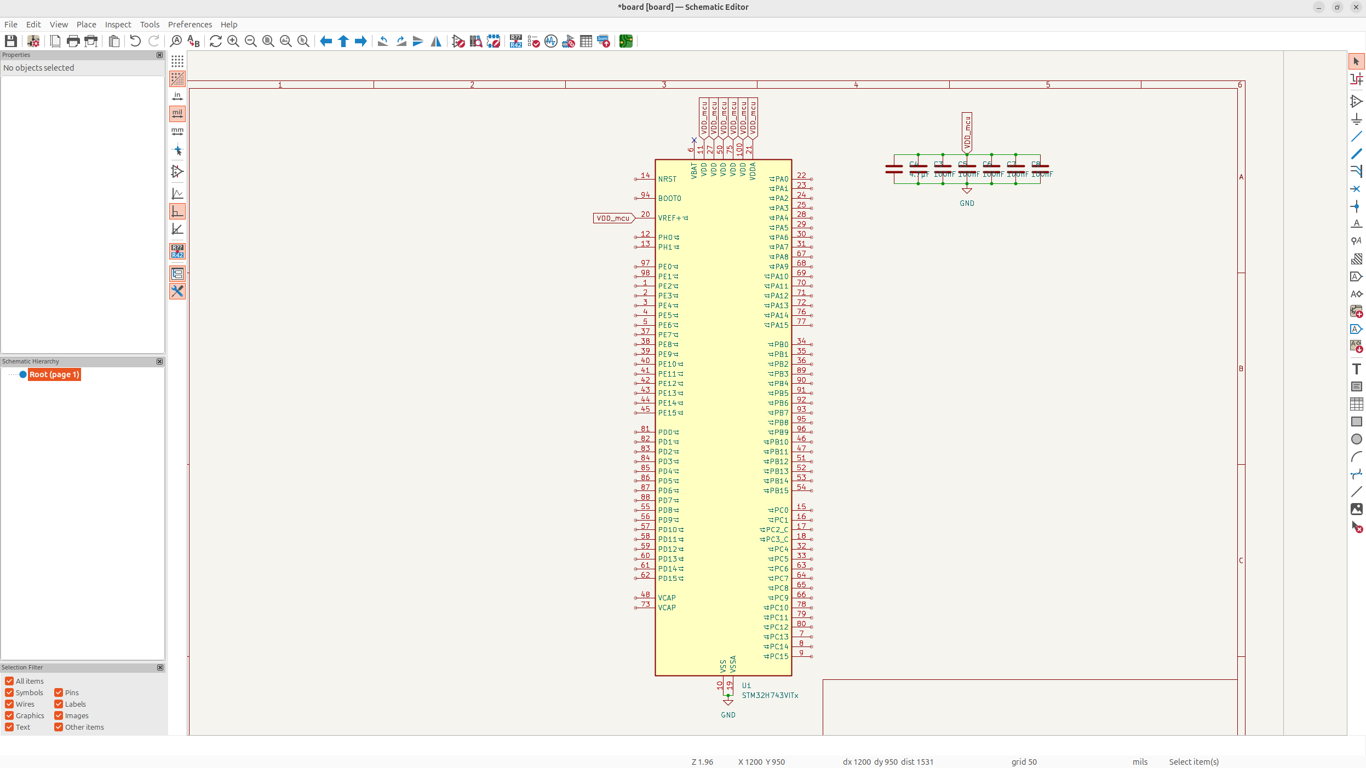
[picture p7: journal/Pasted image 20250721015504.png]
Pasted image 20250721015504.png

Keep in mind, while I'm going through these fast, lots of these decisions take me hours, because I've never done this before and I have to re-iterate.

Anyways, next I forgot, but I need caps on VCAP so that the internal voltage of the chip is alright.

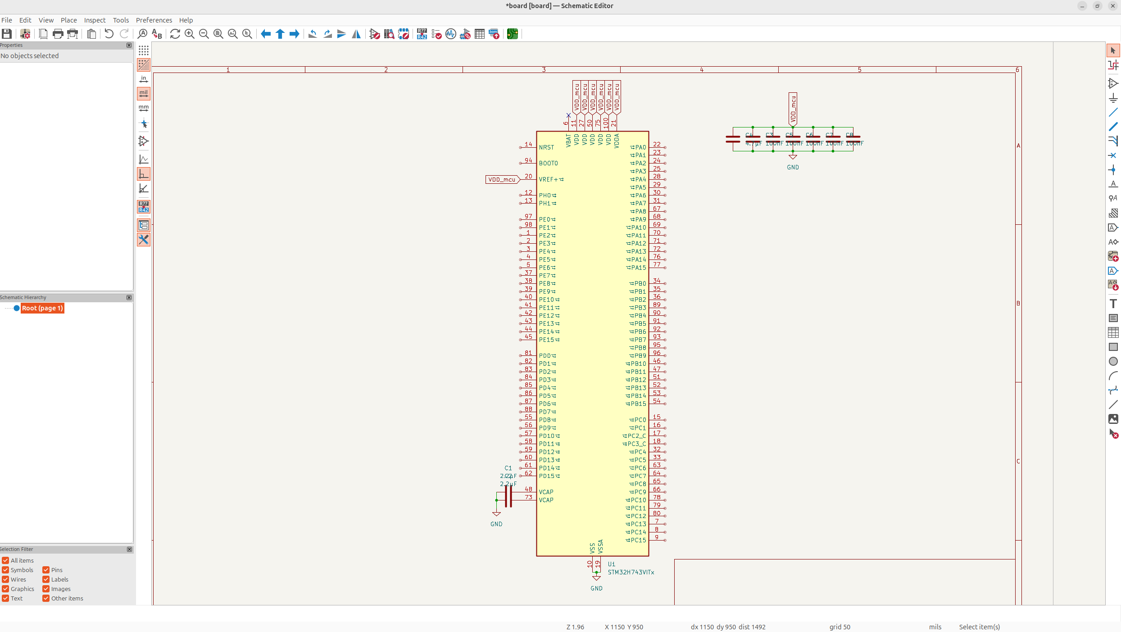
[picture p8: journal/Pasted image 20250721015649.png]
Pasted image 20250721015649.png


And then next, I'll add resetting and booting, which took me a really long time to figure out, but with some friends help, I got it down pretty good.

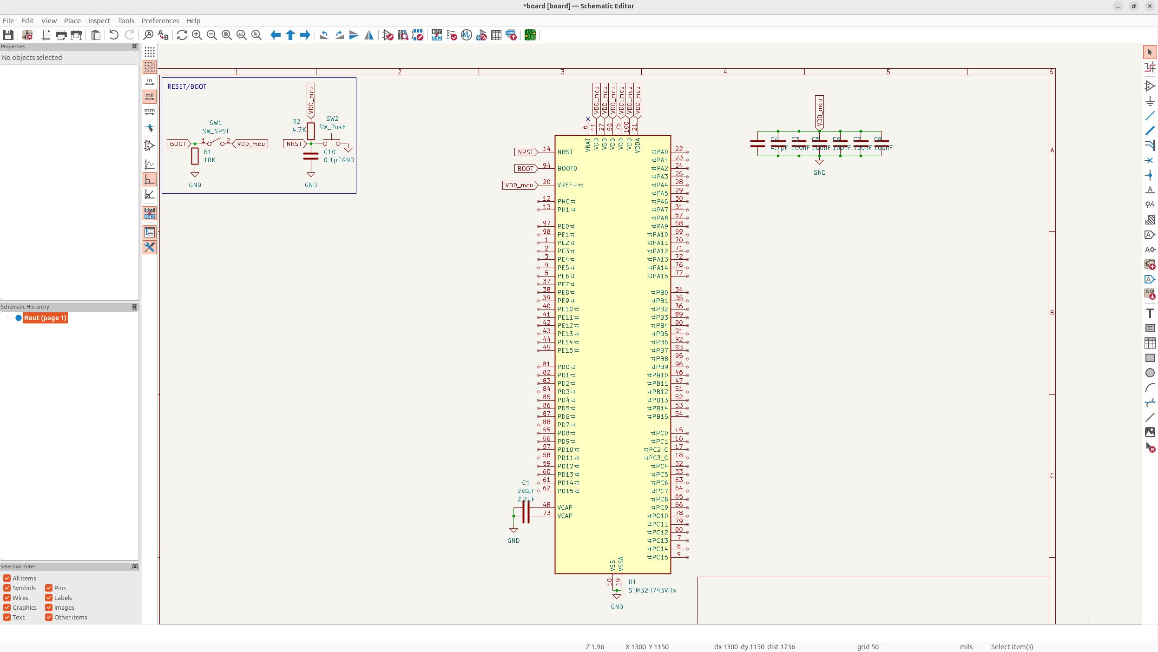
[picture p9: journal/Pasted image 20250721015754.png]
Pasted image 20250721015754.png

And then after that, I need to added my main crystal in. I chose 25 MHz because it's better for USB and ethernet clock accuracy for some complex reason, but it does.

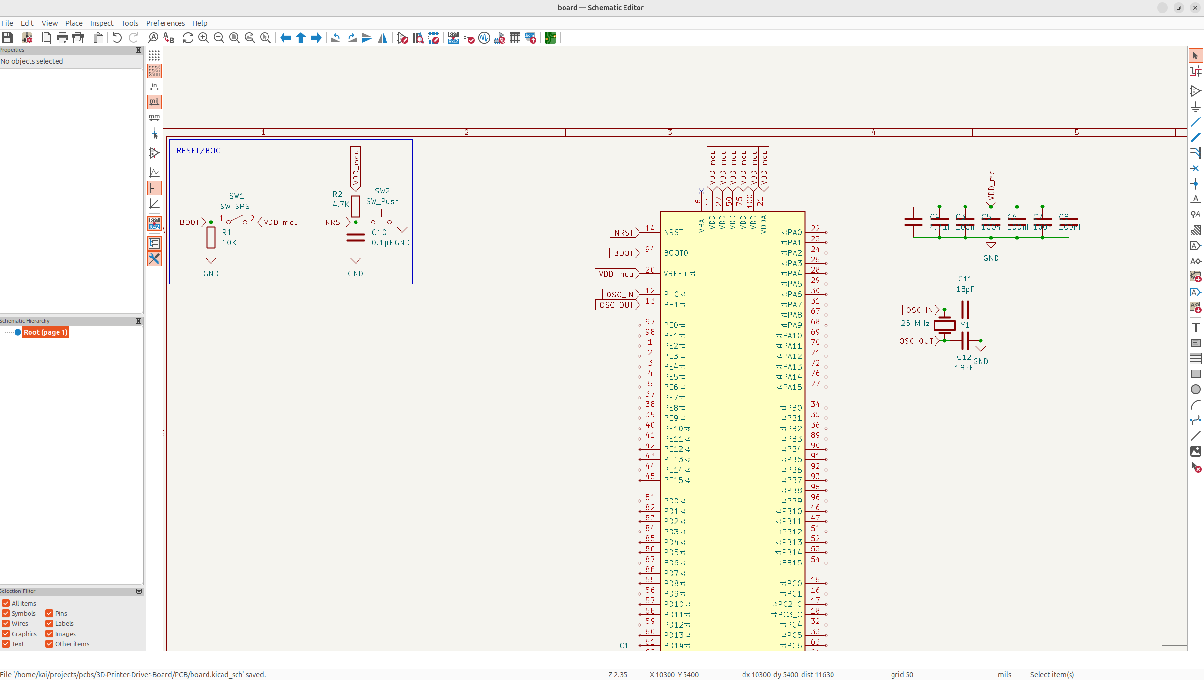
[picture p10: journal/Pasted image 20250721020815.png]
Pasted image 20250721020815.png


## Day 2 - Finishing MCU Schematic - 10 Hours

I got quite a bit of work done on the MCU yesterday, but today, let's finish it off, and potentially we can get started on working on the motor drivers.

First of all, I added Ferrite beads to VDDA so it doesn't receive any noise from the standard power line:

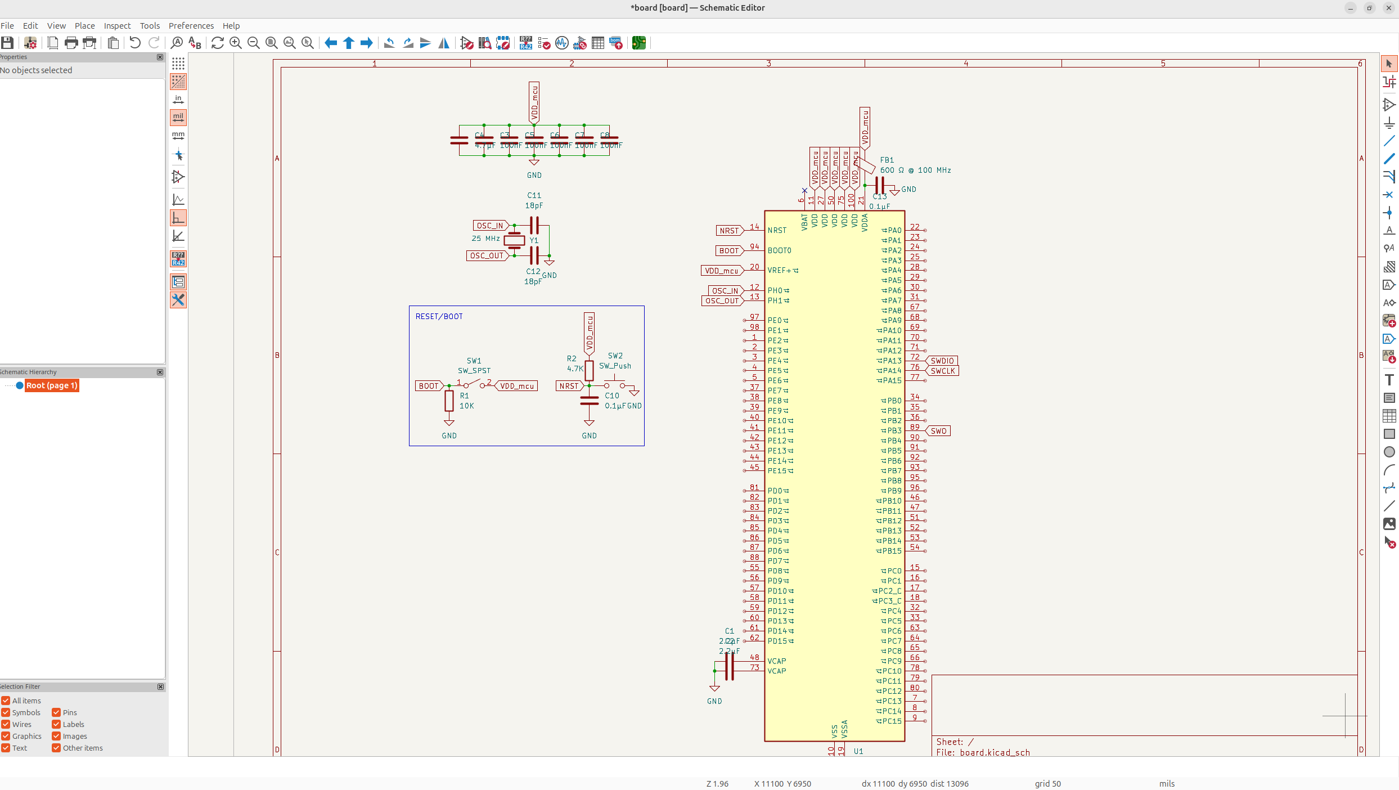
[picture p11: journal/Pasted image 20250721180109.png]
Pasted image 20250721180109.png

After that, I implemented SWD header debugging so I could debug the programming and manually flash and stuff.

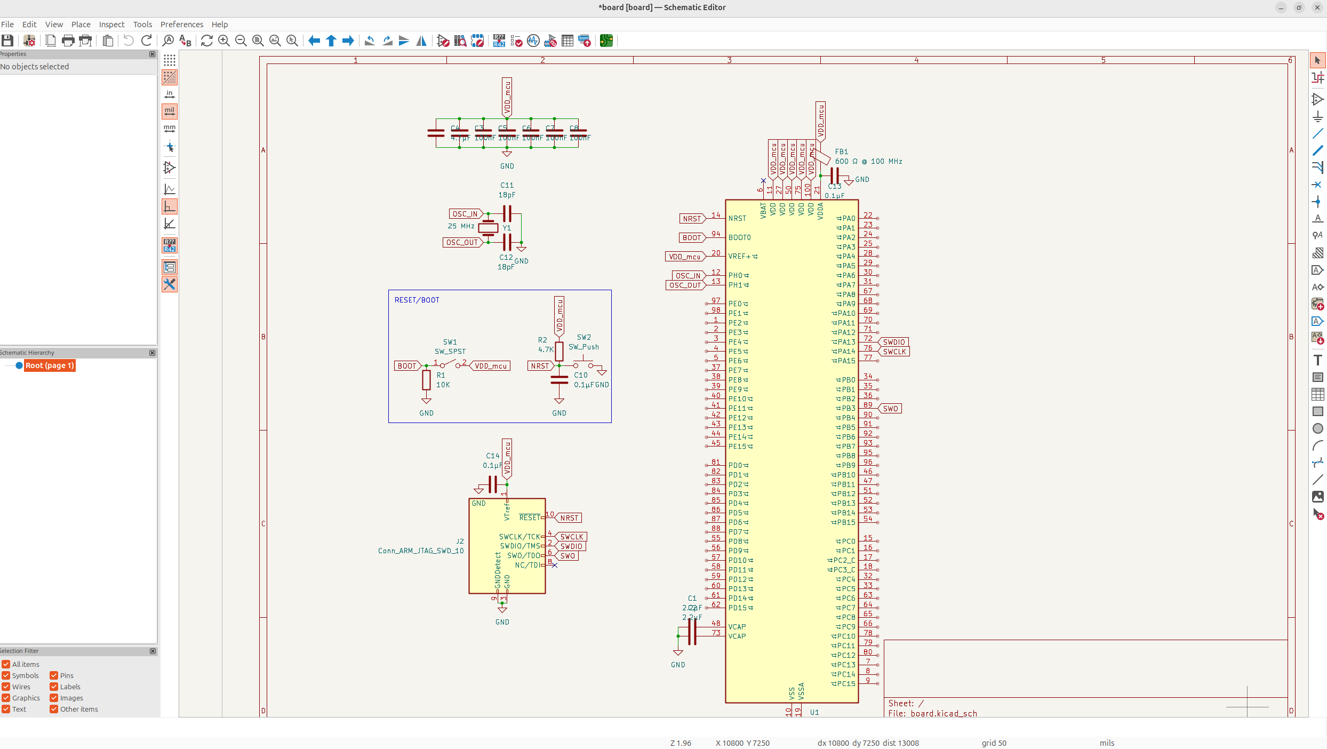
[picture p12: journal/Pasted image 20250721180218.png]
Pasted image 20250721180218.png

Now there's some more things I need on the MCU, but I want to work on the SD Card and USB peripherals. First I'm going to put the SD Card in, because that one made a bit more sense to me, everything is basically data or power/GND and then you just put pull-ups on data's and pull-downs on powers.

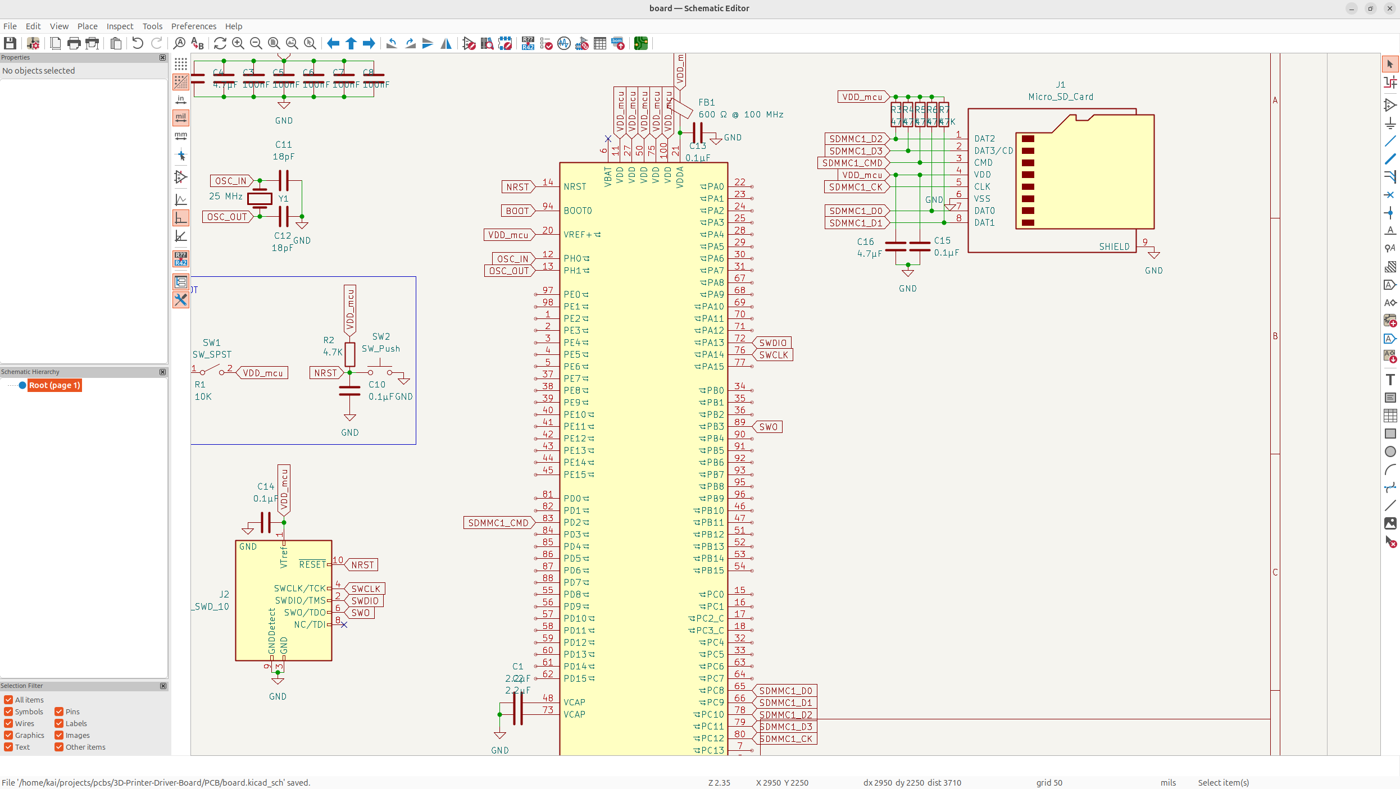
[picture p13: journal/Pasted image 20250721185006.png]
Pasted image 20250721185006.png


And now I just have to add the USB-C and CAN ports, I chose USB because it's pretty modern and there's also no harm in having CAN, especially because it's such a high quality board, I think enterprises will like it.

I'm also going to have it where when the USB-C is plugged in, it's going to power the board, but you can also power it with an external power supply, this is just really convenient for development.

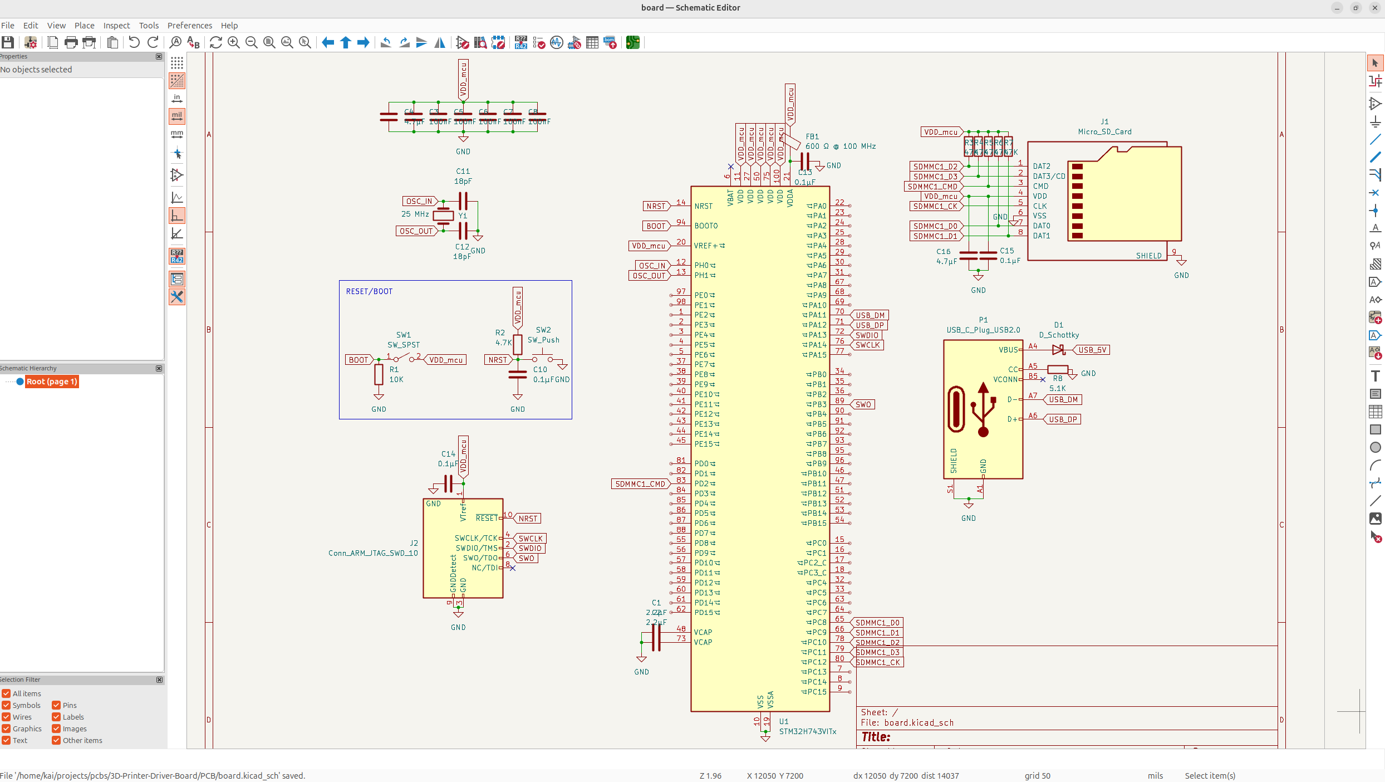
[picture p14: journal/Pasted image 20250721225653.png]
Pasted image 20250721225653.png


The MCU is looking pretty sick now! Time to implement CAN in! But while researching whether to put CAN in or now, I found out that the TMC2209 doesn't actually support it, and instead I need UART. So I actually did finish implementing it, but now I just need to use UART instead so I'm not going to bother.

Something I neglected though, was adding in the PSU input for the board, so let's add that real quick. You'll notice the board is constantly being changed with some new formatting, just because everything is getting bigger too.

And now we have the PSU in the top corner.

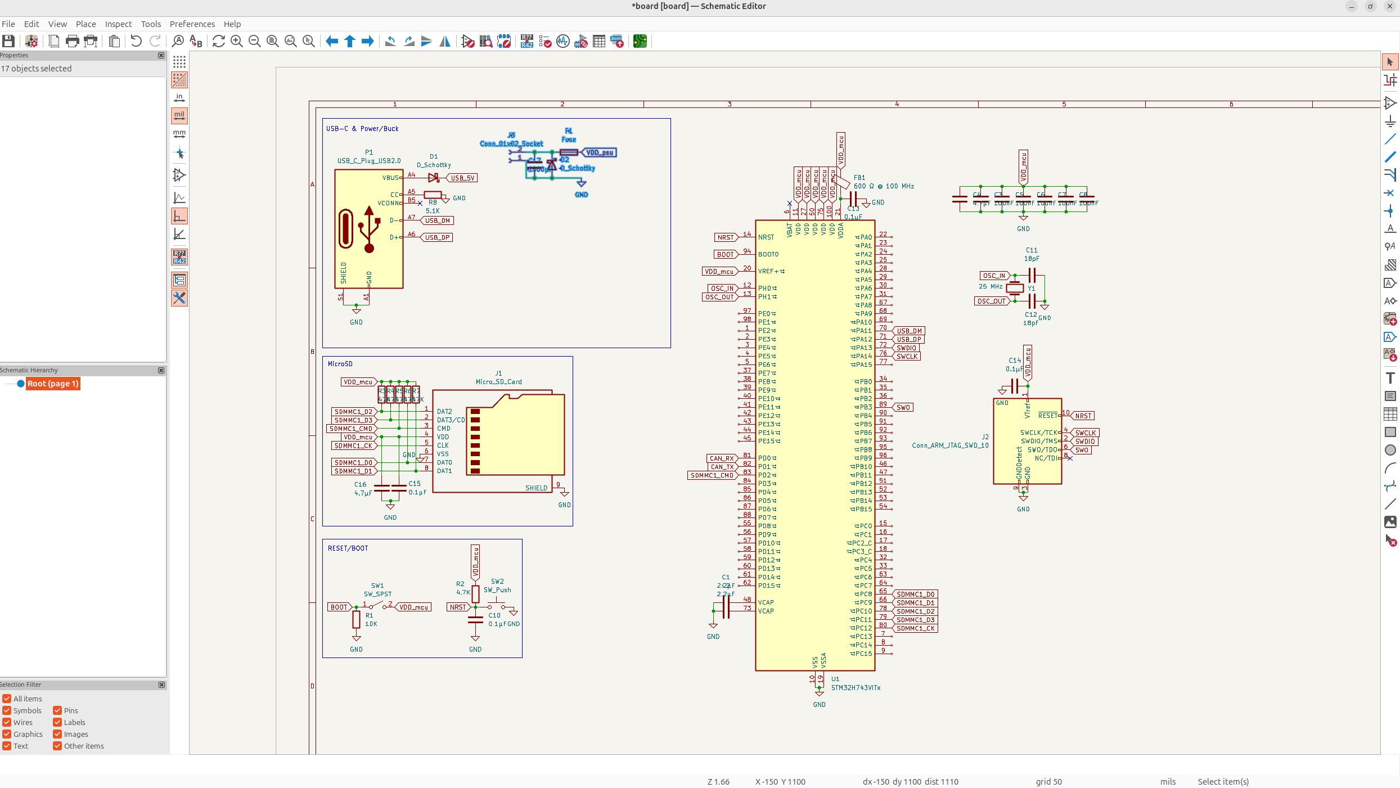
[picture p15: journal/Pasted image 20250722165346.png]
Pasted image 20250722165346.png

It might be a bit wrong, but I'll figure that out in a bit, for now, we need to convert the 12/24V down to 3.3V for the MCU.

It's a bit complicate to wire, but basically just steps down to 3V3, and then stabilizes and protects it using some capacitors and diodes, and then it needs some internal voltage too, which is what the FB pin is for.

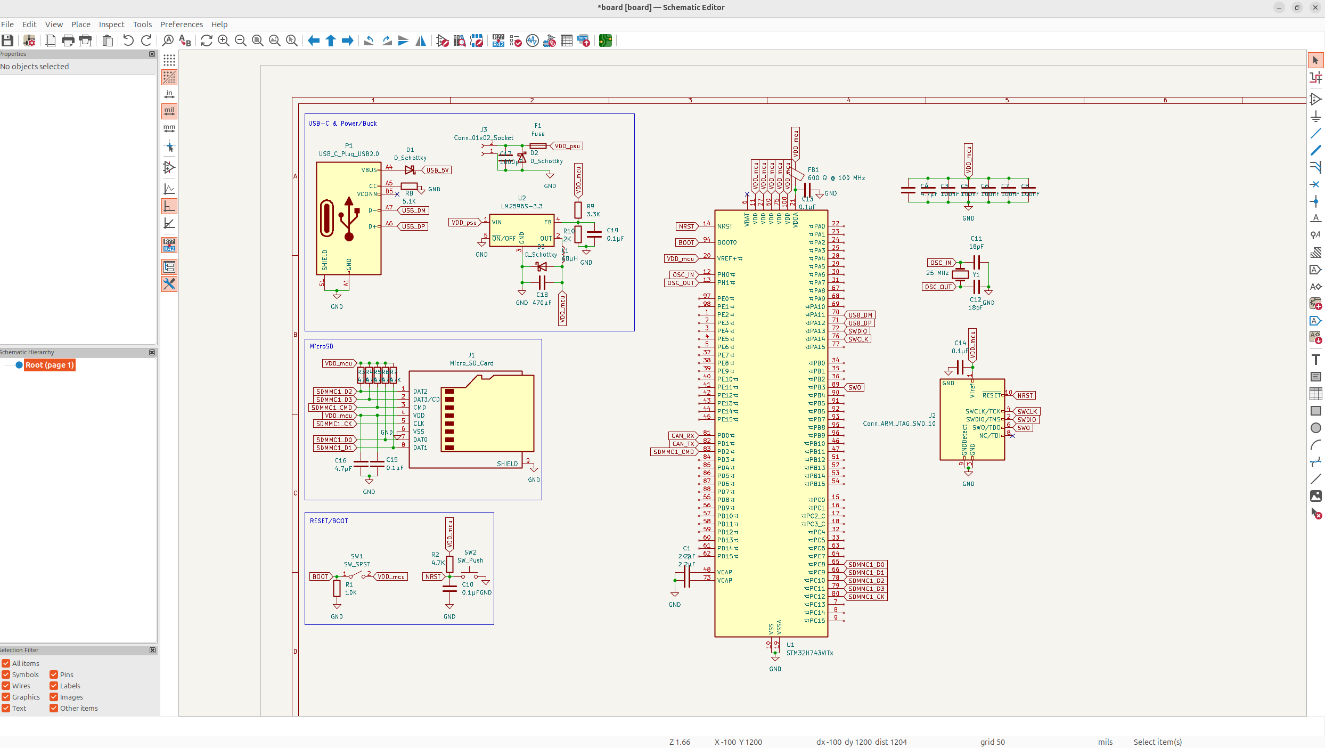
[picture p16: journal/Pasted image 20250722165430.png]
Pasted image 20250722165430.png


And just like that, we have a buck converter for the PSU! But I still kind of need to convert the 5V from the USB down to 3.3V for the MCU, so I might need to re-use the current buck converter if I can, or add another one...

But anyways, after reaching out to some people, they suggest I use a different buck converter because of the bad switching frequency, and also convert to 5V instead of 3.3V and then use an LDO to get from a 5V rail to 3.3V. So after a bit research, I'm just going to use the TPS54331 chip.

So after an absurdly long time, I got the buck converter wired for 12/24V to 5V.

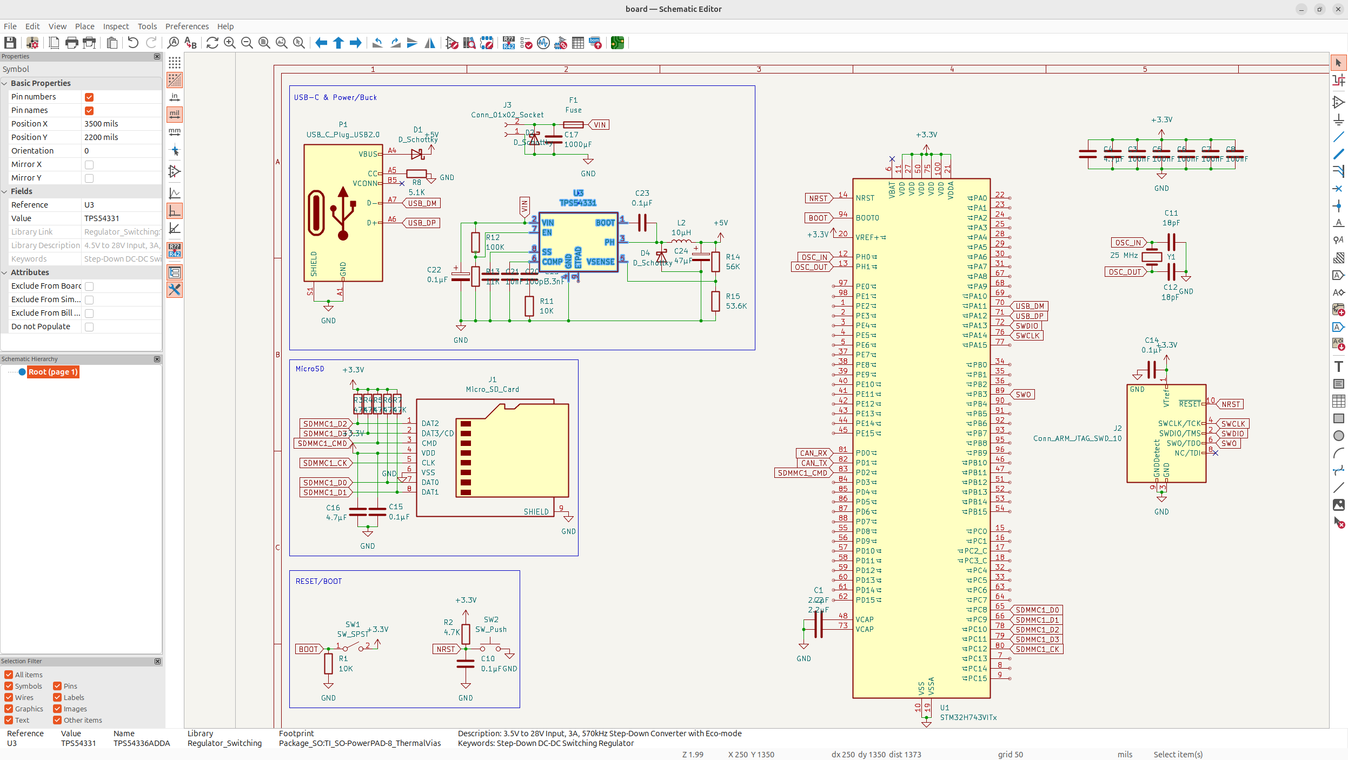
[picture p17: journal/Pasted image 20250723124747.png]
Pasted image 20250723124747.png


I know I don't journal everything I do with this schematic because there's so much stuff, but I'm constantly making iterations, so I also replaced all the new labels with power labels and re-organized some stuff.

Anyways, that's the majority of the MCU stuff wired now. I spent a really long time working on this stuff today, and I got a lot done!

## Day 3 - Power and Drivers - 10 Hours

Today was all about finishing the power schematic, and adding in the stepper drivers and maybe some other things into the schematic.

So first things first, I need to have a common 5V rail. You see, both the USB and the PSU with the buck converter, are going to output 5V, but they can't both output them at once, so I need to output only one of them if they're both on. I'm going to prioritize the PSU, because the PSU also provides a 12/24V power, so it's going to be preferential if they're both connected.

I'll use a simple P-Mosfet circuit:

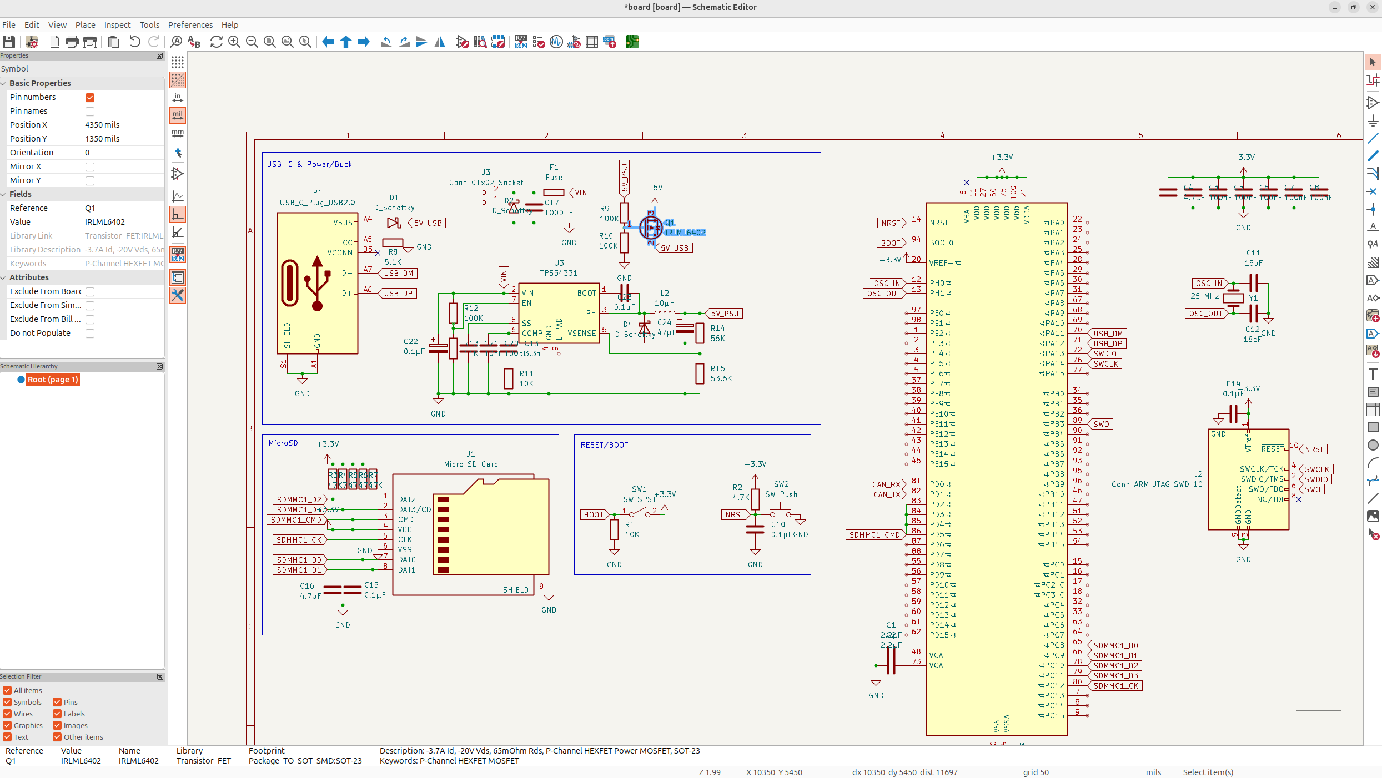
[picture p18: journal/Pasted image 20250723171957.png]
Pasted image 20250723171957.png


And then I need to add a linear regulator/LDO to step down the 5V to 3.3V for the MCU and some other operations. You see, I need the 12/24V for the steppers, the 5V rail for some fan gate and other operations, and then the 3.3V for the MCU and stuff, so it's important that I have all of these rails separate. I'm going to use the same LDO as the Manta M4P, the AMS1117 and then of course decouple it to stabilize the voltage.

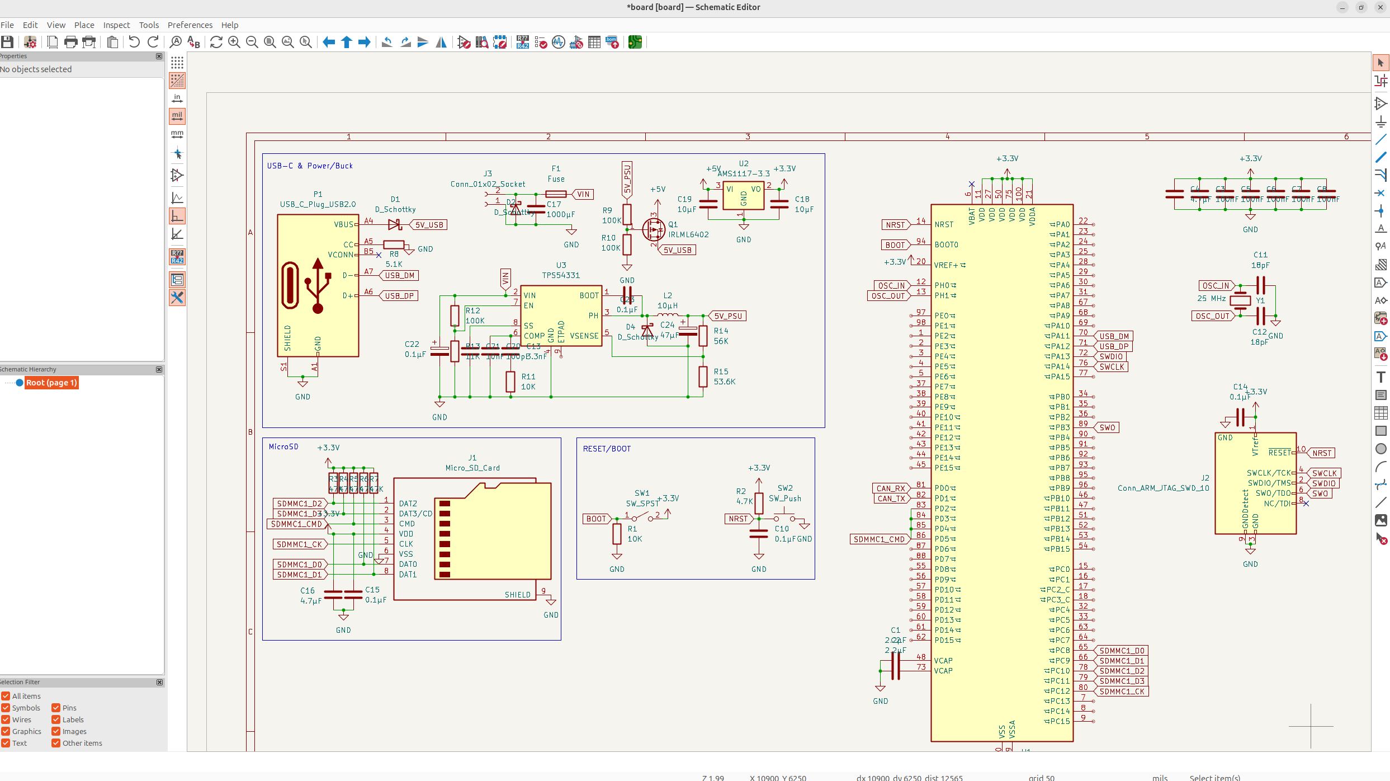
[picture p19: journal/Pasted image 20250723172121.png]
Pasted image 20250723172121.png


Now... we can finally get to working on the stepper drivers! The MCU and power is finished so let's add the X driver, I'm going with stepstick, because I like how easy it is to assemble and it has a bunch of extra features which are nice, and it looks sick on boards instead of using an onboard chip.

So let's add the first motor driver... it's a bit tough to wire, but I think this should be good. I'm using UART to control everything and then I expose it to a 4 pin connector for the steppers.

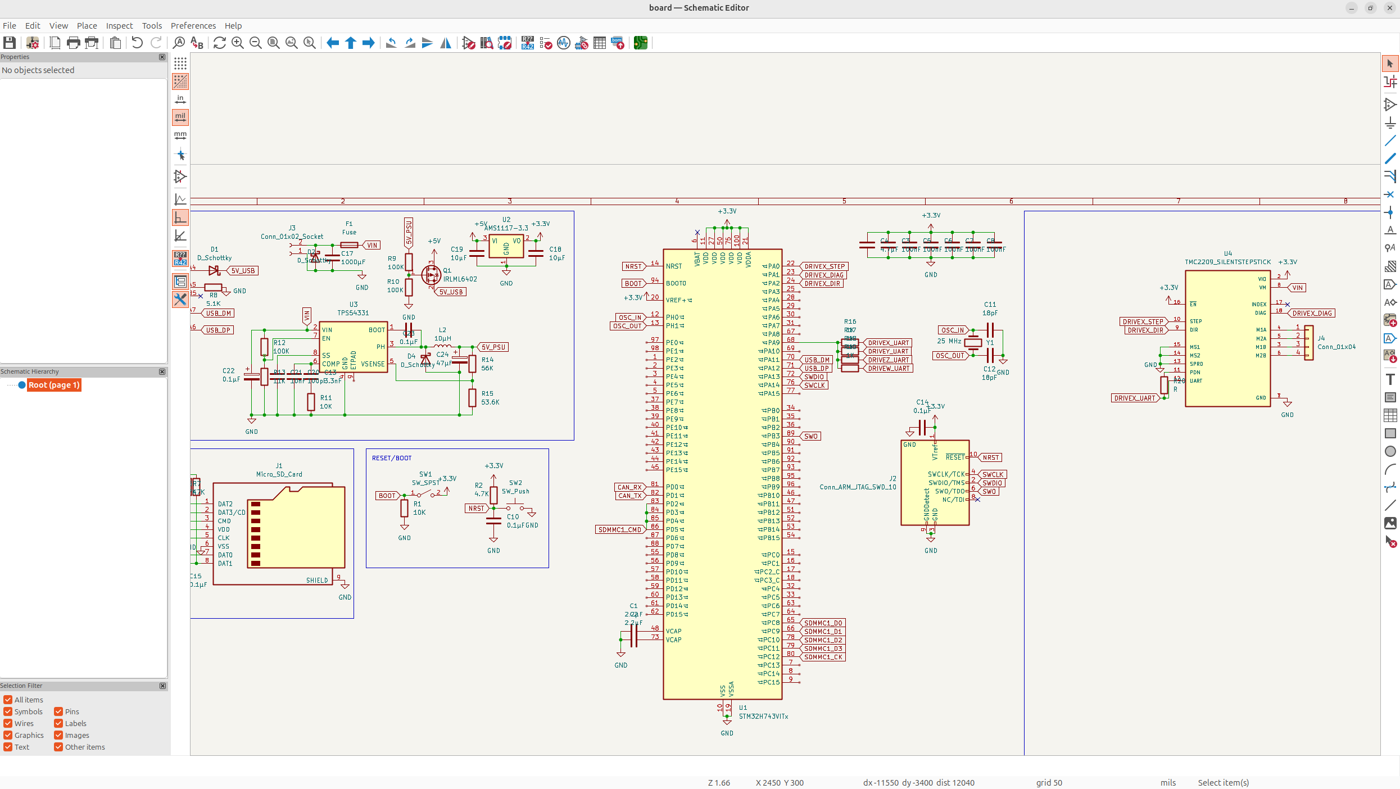
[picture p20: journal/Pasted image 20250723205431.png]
Pasted image 20250723205431.png


Now I'm going to add the endstop pins... I want to be able to switch between sensorless and endstop homing, so I'm going to include both of them, just as separate GPIO's. The Manta M4P does a jumper switch approach instead, but I'm not low on GPIO's, so I feel like controlling this in firmware is more convenient.

While adding the endstops, I also fixed the wiring for the TMC2209 silent step stick, because I was basically wiring it for the IC instead of the module, and I also added caps and pullups/pulldowns and whatnot.

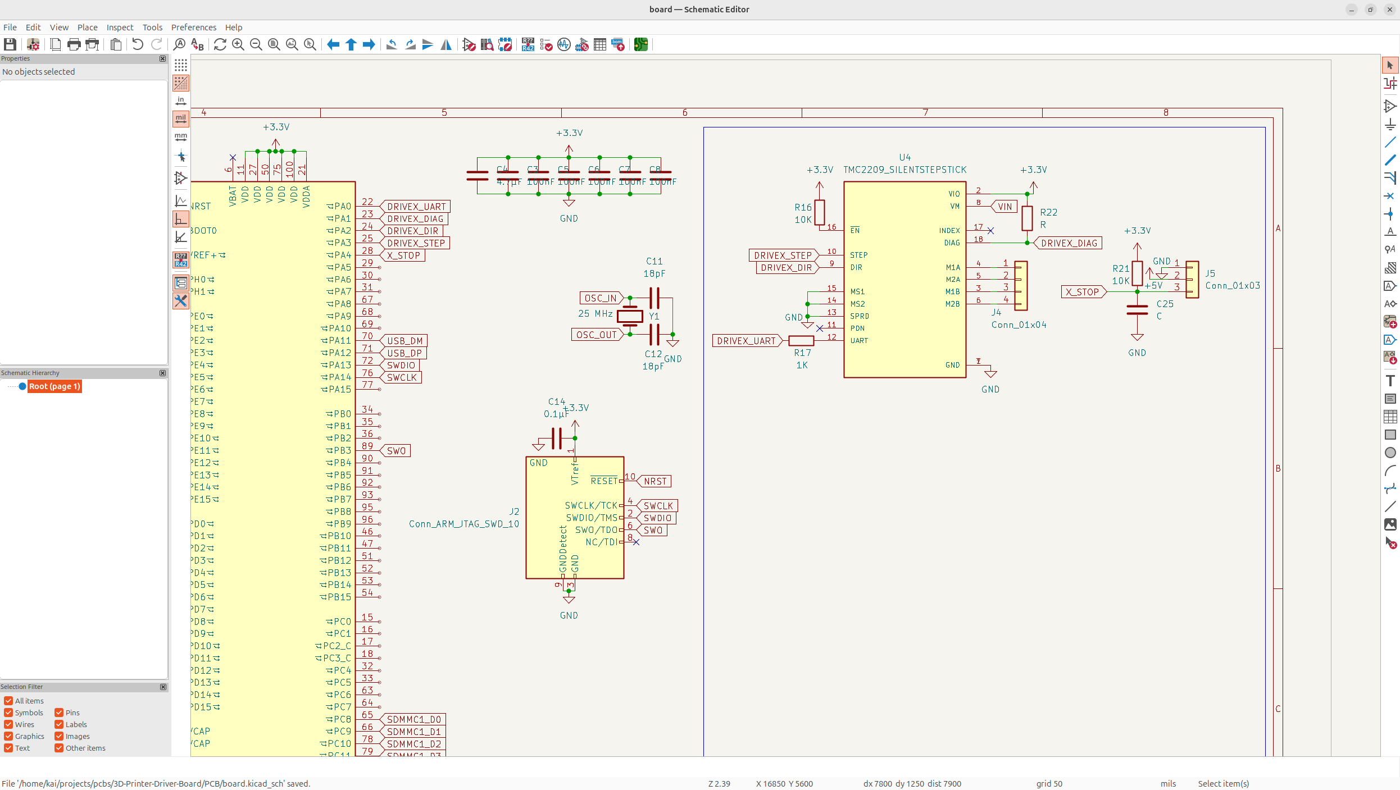
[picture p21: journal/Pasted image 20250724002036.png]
Pasted image 20250724002036.png


And then I kind of forgot to add decoupling caps on the power pins so here:

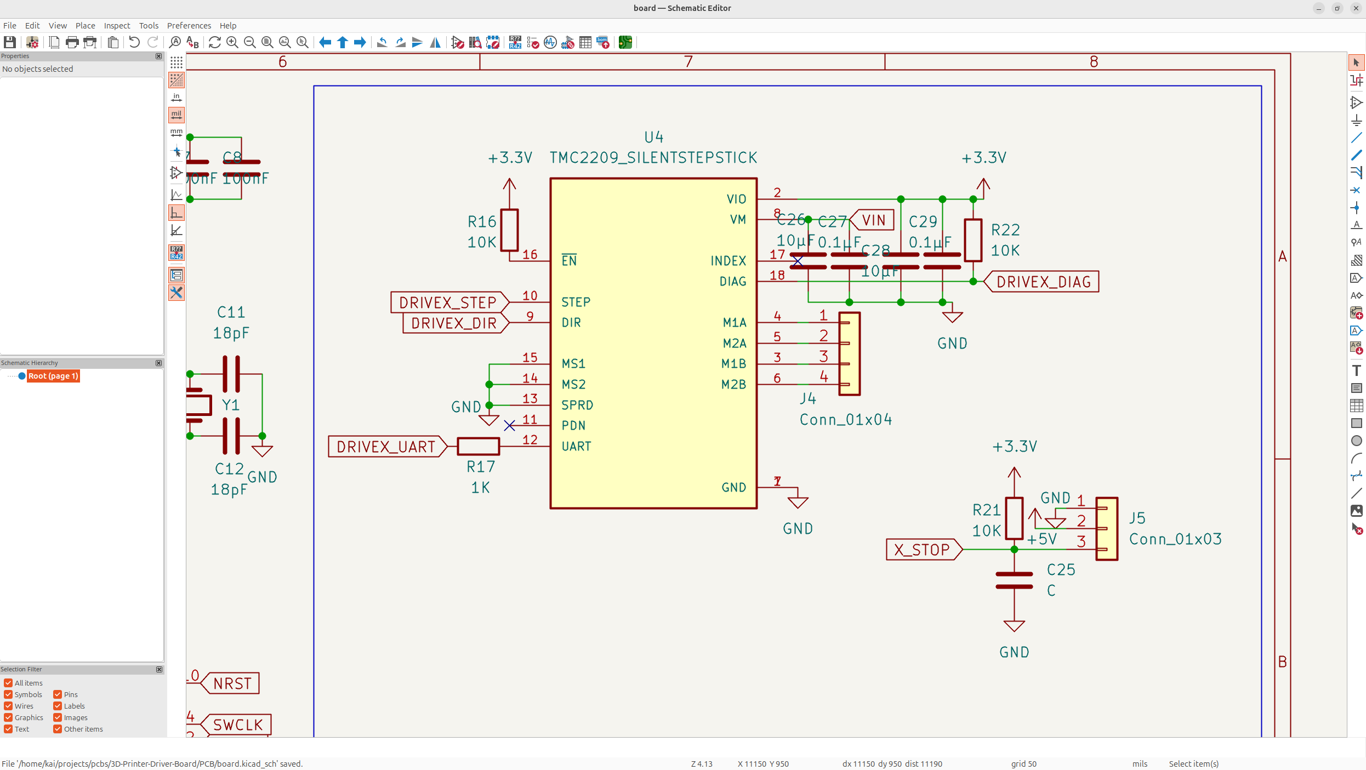
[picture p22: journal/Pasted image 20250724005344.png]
Pasted image 20250724005344.png


And then after that, I looked into it a bit more, and I messed up the single line UART, you need to converge both the RX and TX UART pins to one line, but I was just using one IO.

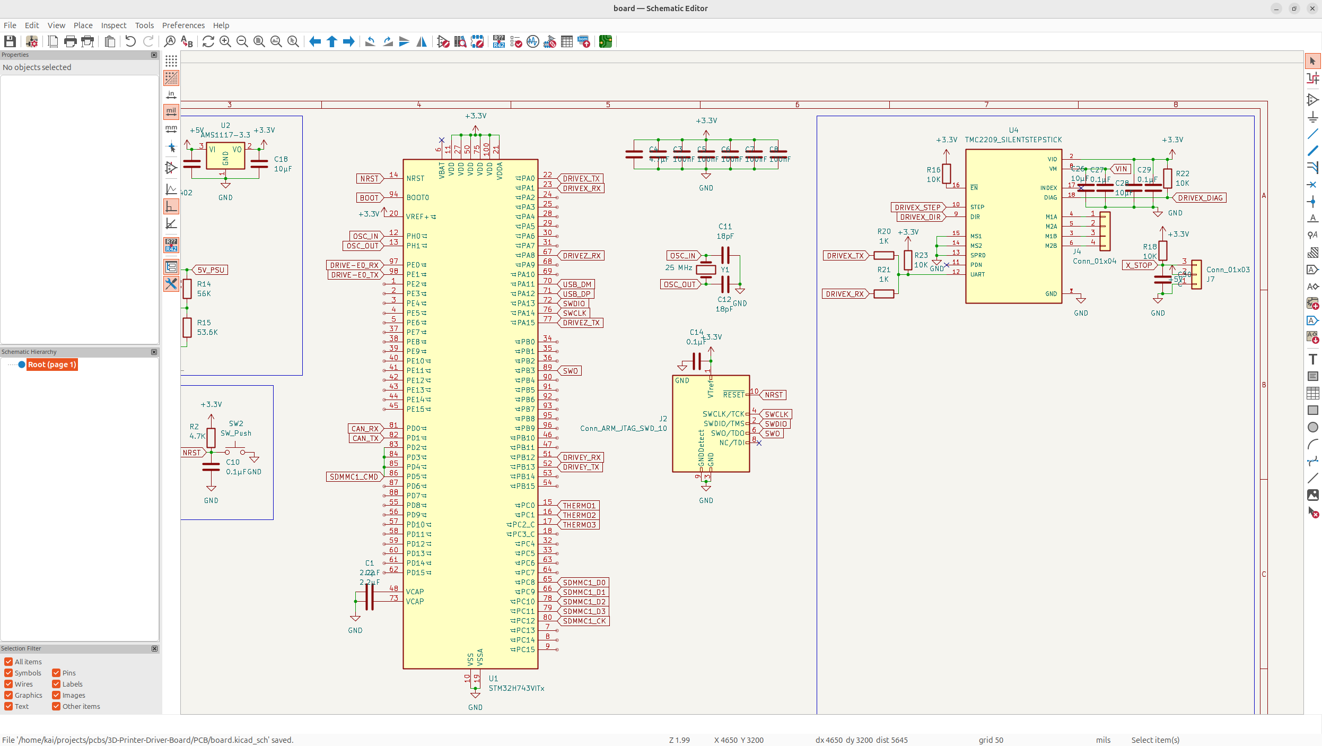
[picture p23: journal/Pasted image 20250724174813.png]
Pasted image 20250724174813.png


After that, I planned out all the UART pins on the MCU so I didn't use them up accidently.

Now, I'm like 85% confident that the schematic for the motor driver is functional, so I'm confident enough to clean up the schematic, and add all 4 drivers in (x, y, z, e0).

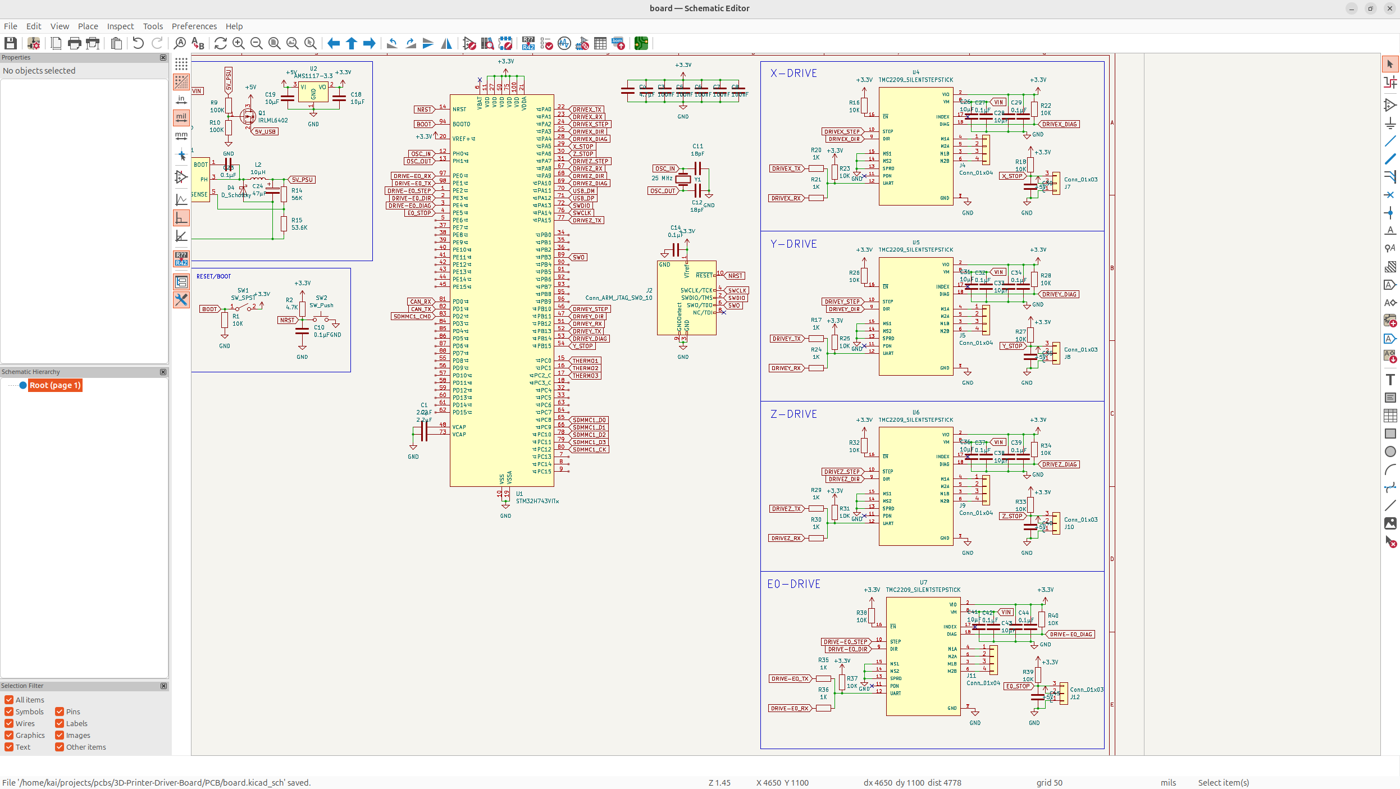
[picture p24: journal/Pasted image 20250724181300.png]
Pasted image 20250724181300.png


Now the schematic is looking INSANELY cool.

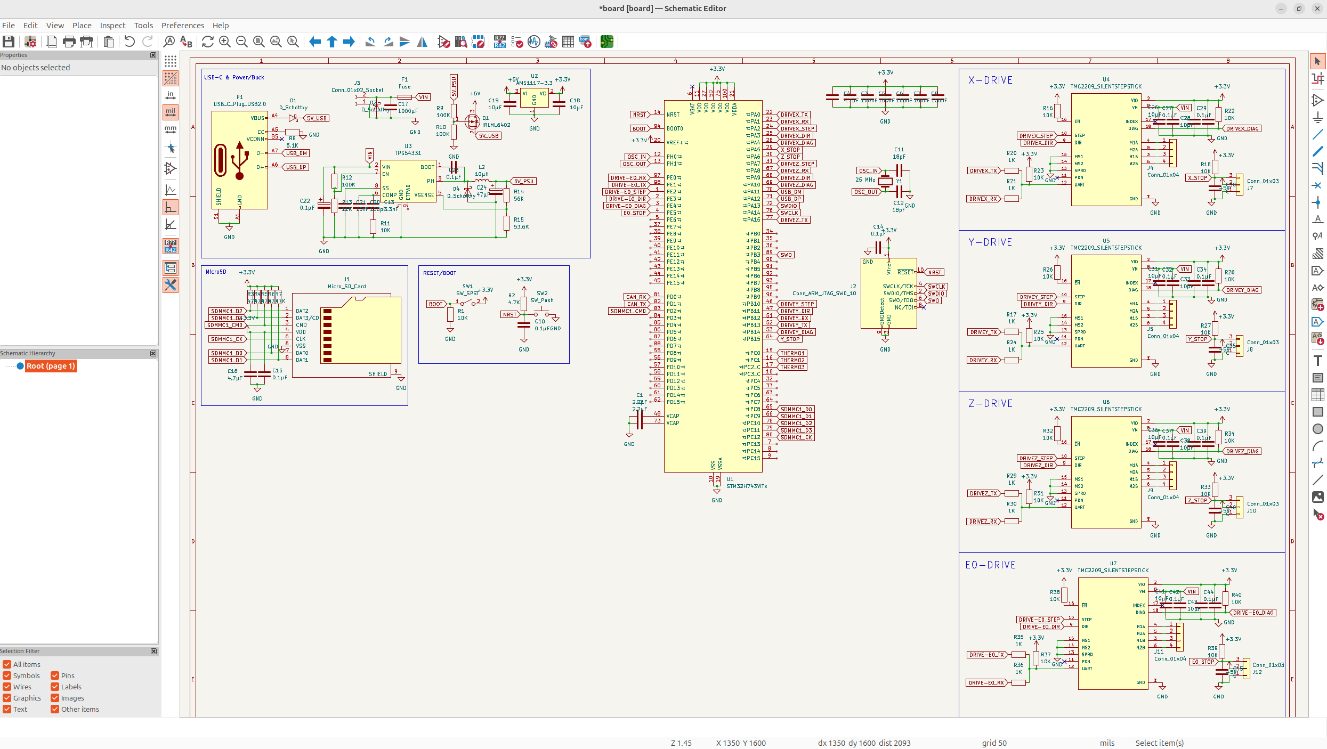
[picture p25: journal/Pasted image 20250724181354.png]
Pasted image 20250724181354.png


Now this day actually took me a really long time, because the motor drivers kept on having to be re-iterated on, and the parts were pretty complicated. At least I finally have the main part of the board on, so I can kind of get to adding features I want.

## Day 4 - Funtime :D - 10 Hours

Today was all about adding cool features I want on the board like fans, thermistors, etc.

All the wiring should be easier from here on out happily, but I still need to be wary about protection and stuff.

So first thing I'm going to add to the board, is the thermistors. I've decided on going with 3 thermistors because if people want more, they can always add an I2C bus, but most people aren't using more than 3. The connector is just GND with an IO pin, with some pullups and a protection for transient voltage spikes/surges.

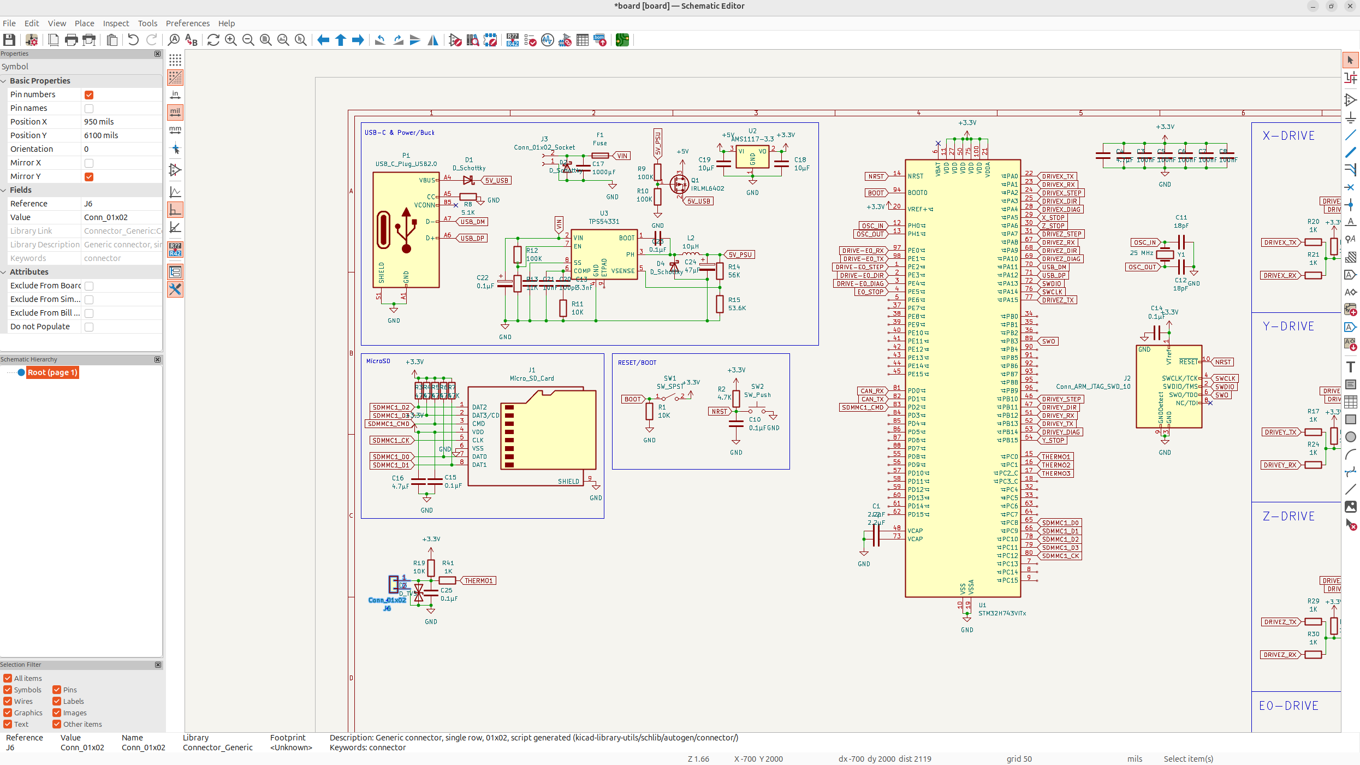
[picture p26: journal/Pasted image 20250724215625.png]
Pasted image 20250724215625.png


Now I can just multiply this for the 3 thermistors I want:

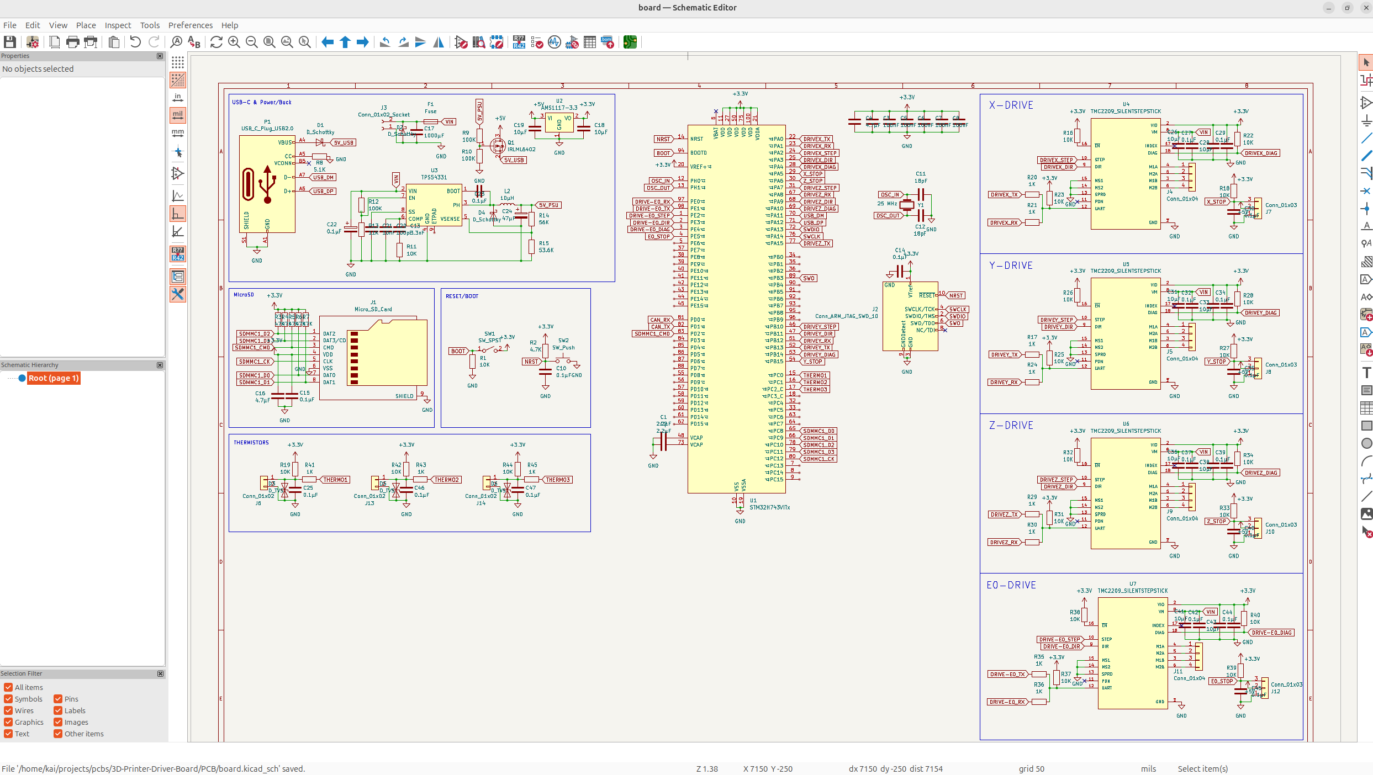
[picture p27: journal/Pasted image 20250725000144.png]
Pasted image 20250725000144.png


Next, I'm going to add a connector for a servo port, because people sometimes like to have a servo for things like a bed leveler or a filament changer.

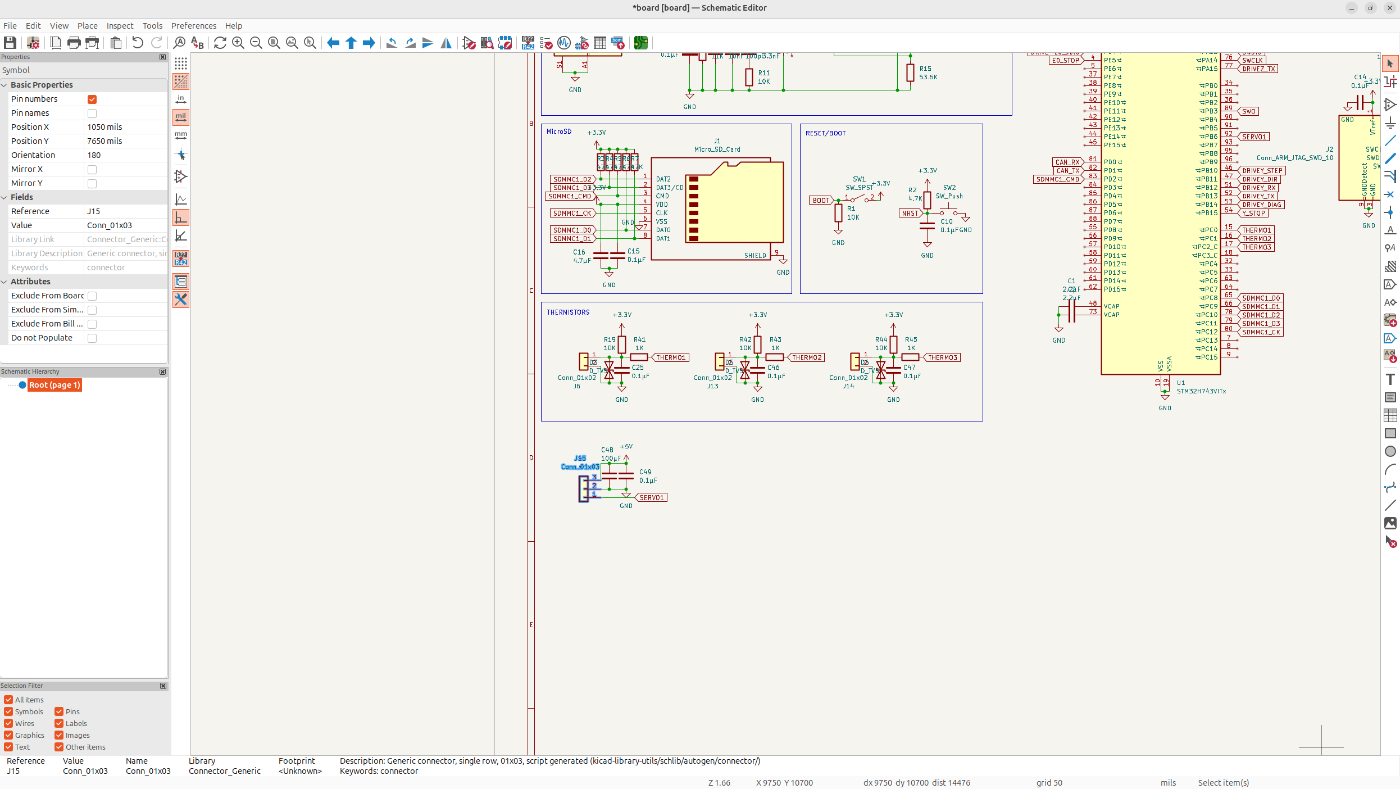
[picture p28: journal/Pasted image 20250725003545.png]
Pasted image 20250725003545.png


And then I can do this cool thing, where I add an inductive probe connector, but this also functions as a BLTouch port using both the servo port AND this inductive probe connector, so it's like a triple function.

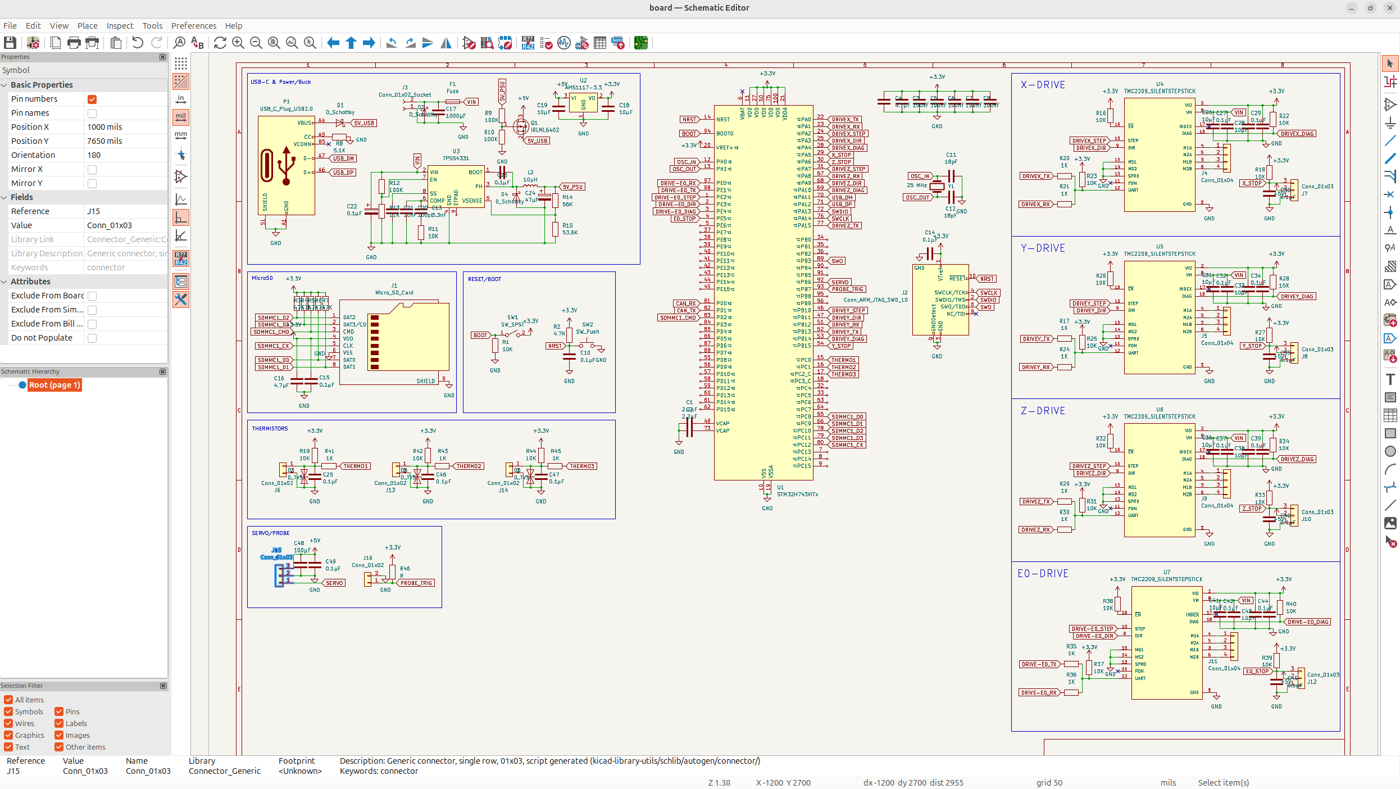
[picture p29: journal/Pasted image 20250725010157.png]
Pasted image 20250725010157.png


Now I need to implement SPI on my stepsticks. Now this took me nearly 5 hours to figure out and implement, and I still think it's a bit wrong, but it's the right idea. Basically lots of TMC drivers only support SPI instead of UART, so you need to support both and be able to switch between them.

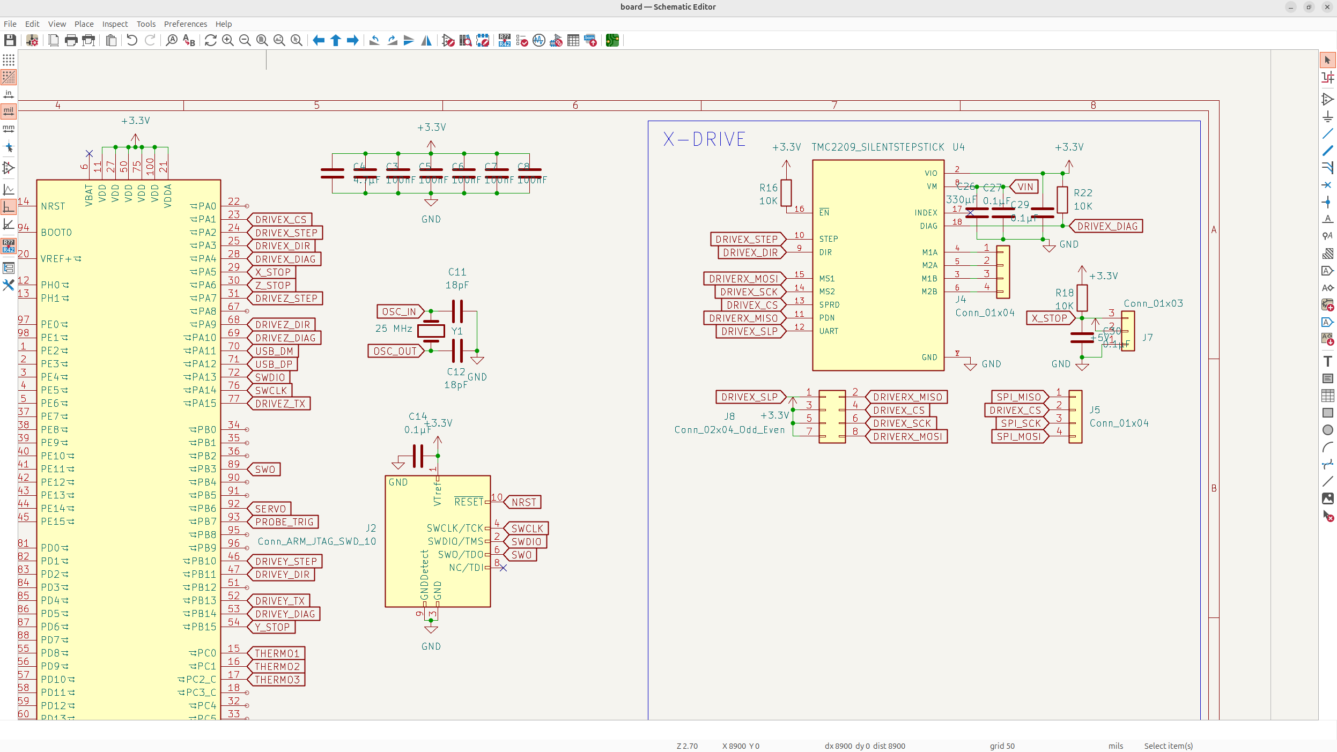
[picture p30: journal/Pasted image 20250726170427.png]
Pasted image 20250726170427.png


And I'm just going to end off there because that took me so long to understand and figure out.

## Day 5 - Touch-ups and Features - 6 Hours

Now, I've figured out the core board, and I can add some more features like TFT and LCD screens and some other things.

So first I implemented a TFT display using UART:

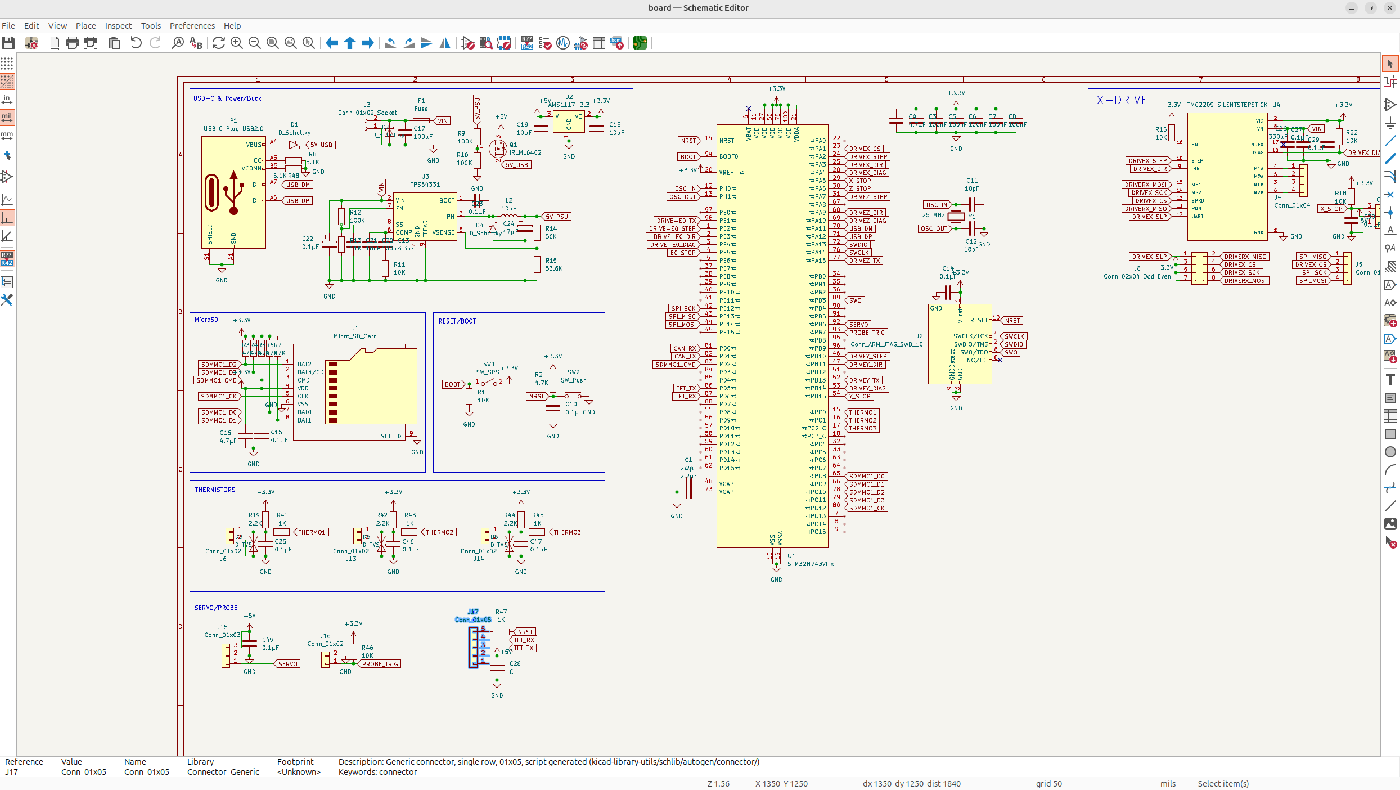
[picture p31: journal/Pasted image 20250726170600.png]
Pasted image 20250726170600.png


and next, I wanted to be able to support LCD. I want to support SD cards too, so I need a connector for SD card LCD and normal parallel LCD displays, so I have to make 2 like so:

It took a really long time to figure out which pins needed peripherals and fitting them onto the MCU, but I got it down pretty nicely:

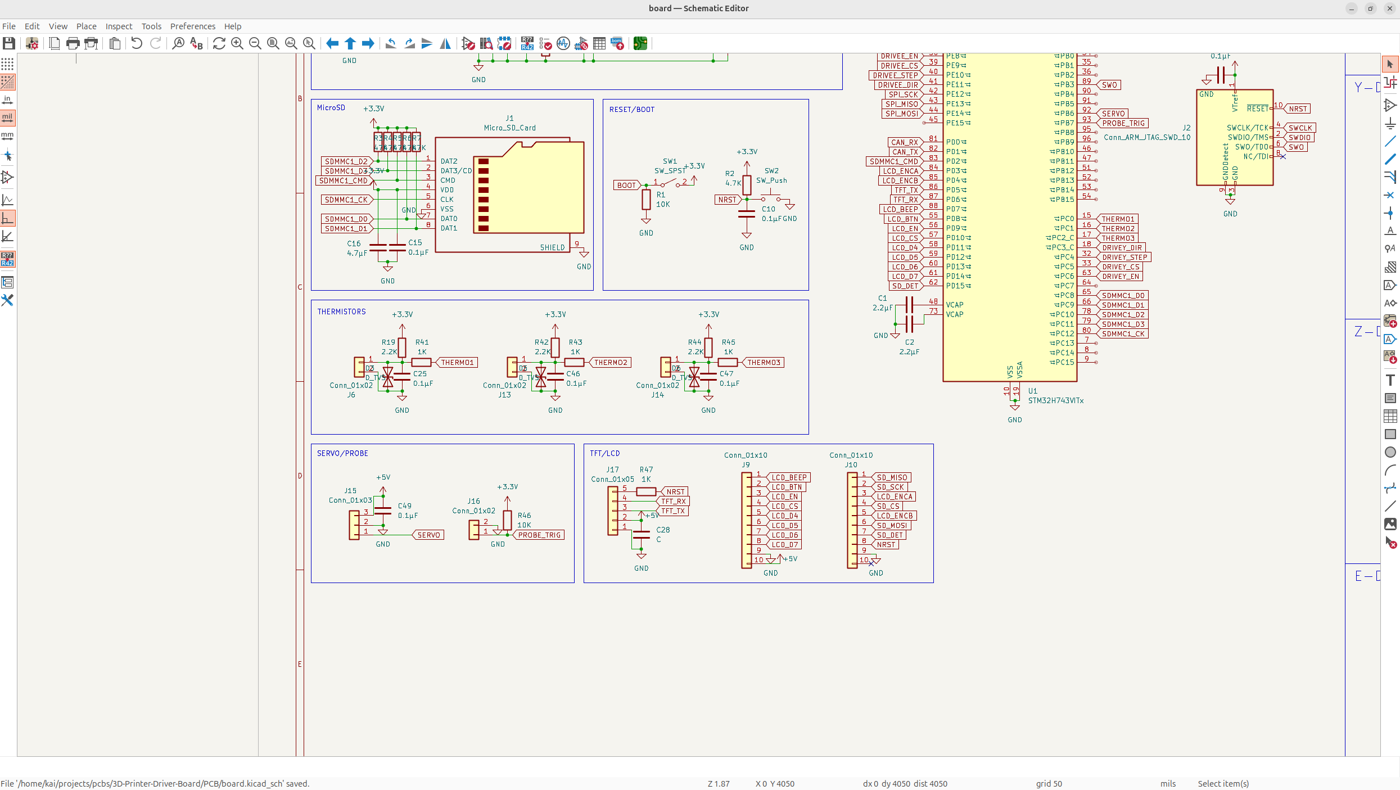
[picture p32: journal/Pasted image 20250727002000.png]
Pasted image 20250727002000.png


And now, I needed to refine my drivers even more. I wanted to add a jumper so that I could toggle between endstop and sensorless homing, so I only needed 1 label which would free up my MCU a bit better. I also needed to add EN apparently, so I wired that in too and cleaned up my SPI.

Not just that, but I also added all the drivers, all this took me a pretty long time, but I'm just summing it up:

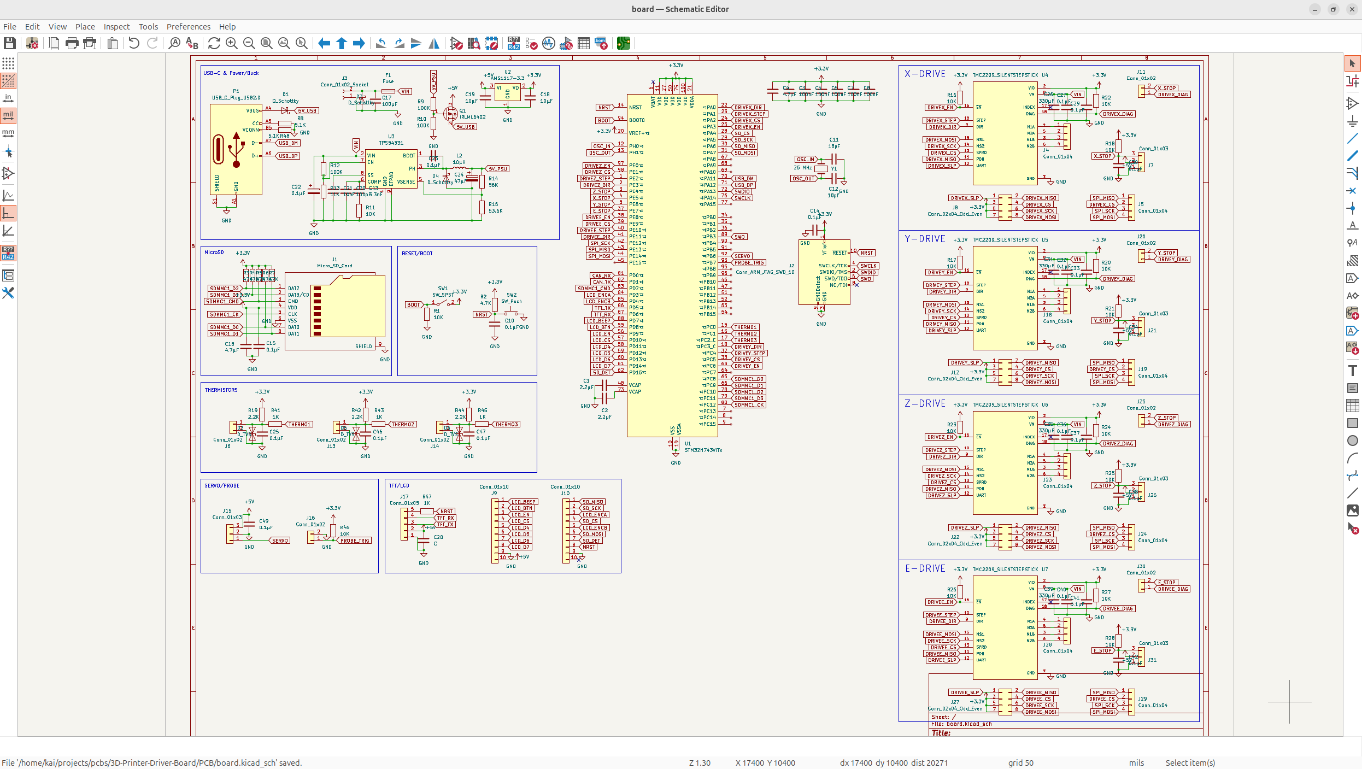
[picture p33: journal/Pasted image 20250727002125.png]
Pasted image 20250727002125.png


This is the new connector that can toggle homing:

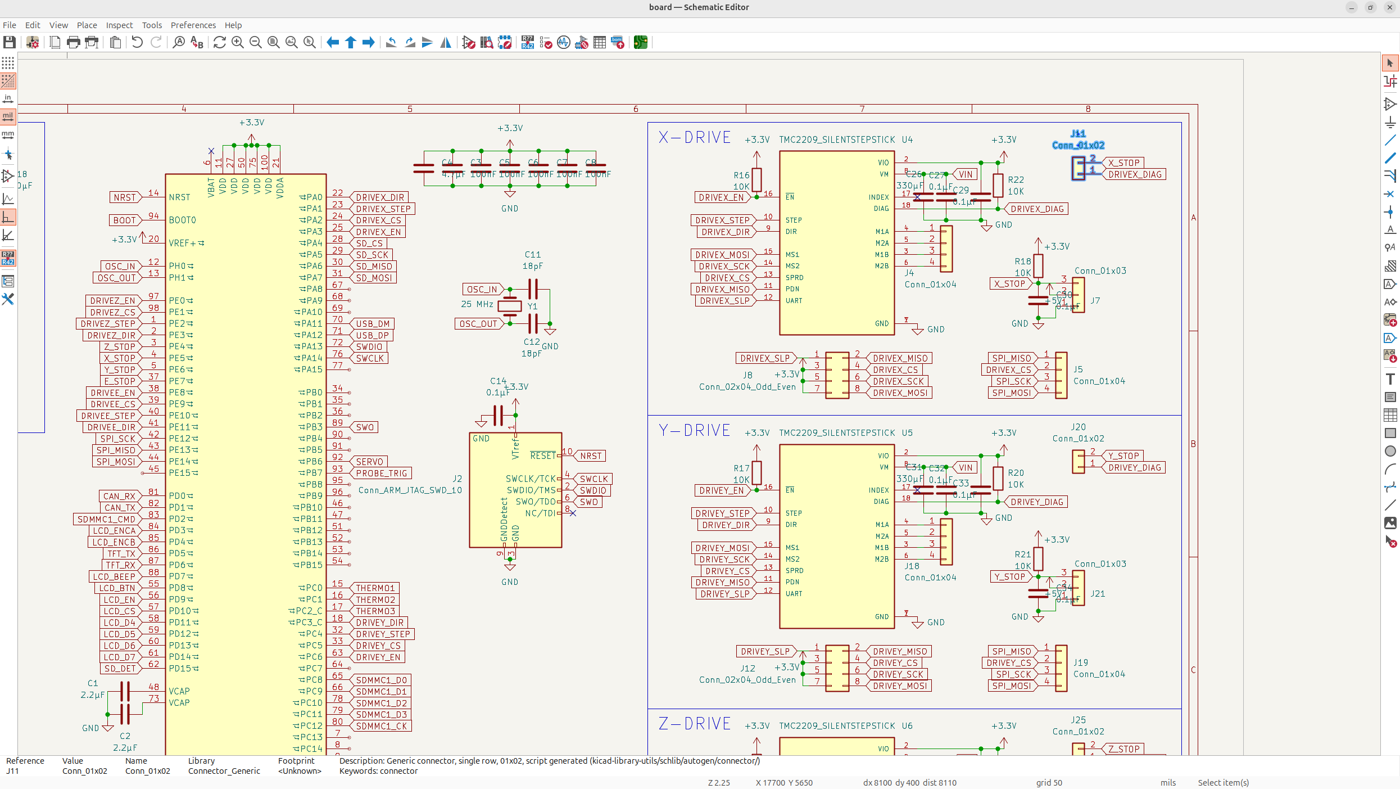
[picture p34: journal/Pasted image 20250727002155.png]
Pasted image 20250727002155.png


It's pretty simple, it just bridges the endstop GPIO, and then you just configure it in software to disable the endstop.

I've been constantly iterating and stuff while doing this, so all of this is taking much longer then how I'm putting it...

Anyways, now I have a feeling I might need some pullups/pulldowns in some places? But aside from that, that's pretty much all the main features on the board I was aiming for, which is amazing!

And of course I was right, I was missing some pullups on the LCD displays, so I added that alongside a small decoupling cap:

Pasted image 20250727005416.png

## Day 6 - Finishing the Schematic - 10 Hours

Now, the only thing I really need on my board is the fan ports and potentially some protection circuits/fine tuning?

So now let's add in the fan connector... I want to support PWM control which allows fine control of the fan speed and whatnot, so I'll probably need a larger connector.

Anyways, PWM is a bit chonky, so instead I'm going to use this cool switching circuit that basically like quickly turns the fans on and off to kind of replicate PWM but worse but it's smaller which I kind of like and I don't really need precision for a 3D printer.

Pasted image 20250727021323.png

And then, after that I just added the basic wiring for the heating elements. It's the same as the fans, but the heating elements draw a LOT more current, so I might need to wire them a bit differently than what I currently have? But I'm not too sure...

Pasted image 20250727024944.png
Pasted image 20250727025002.png

But anyways, now I could finally work on adding footprints to every single part. This took me about 3-4 hours, but I got every single one except the motor stepsticks. Here's the basic protocol I got it down too:
- Small (0.1uF) decoupling caps get 0603 capacitor footprints
- Medium (>1uF) decoupling caps get 0805 footprints
- Larger ones (>10uF) get electrolytic capacitors varying in size
- Resistors with large current get 0805 footprints
- Resistors with small amounts of current get 0603

And then everything else was pretty much fully custom. The different connectors took a bit because you have to figure out the exact connector each thing is, and you don't really want to mess it up:

Pasted image 20250728003242.png

Now I just needed to add the footprint for the TMC stepsticks, which I think need to be fully custom, but I'll see when I research a bit more.

The TMC stepsticks took about an hour and a half, but I got a pretty nice footprint, and the tolerances are only like ± 0.015 mm which is nice.

Pasted image 20250728015530.png

Now I can just add this footprint in, and my schematic will be finished!!! I also fixed up some other footprints to handle some of the crazier loads, but this schematic looks beautiful!

Pasted image 20250728021721.png

And then finally, I had to add the footprints for the displays... AND EVERYTHING IS FINALLY DONE!

Pasted image 20250728171131.png

## Day 7 - The PCB - 10 Hours

Now today was about starting the PCB! I imported all the parts into Kicad but then noticed that lots of the parts weren't right. Specifically connectors and the crystal. The crystal had the wrong pinout and the LCD connectors were wrong. 

So I spent about 2 hours just fixing all the minor issues with my board and then got to the real stuff. First I distributed all the components so that similar components were by each other:

Pasted image 20250729004812.png

This gives me a solid idea of where everything goes, and if stuff is right or wrong. Next I worked on the MCU, now this is my first time organizing components for an MCU so I needed a lot of help from some people, but this is where I got so far:

Pasted image 20250729004906.png

I think it's pretty good, but of course later, I'll ask for some suggestions from some people. 

Anyways, after that, I aligned all the motor drivers together, took me a solid 2 hours or so to get used to layout tools, but I got it pretty nice and precise:

Pasted image 20250729020705.png

Now before I did more work on this, I posted this in Kicad and Reddit and got lots of good suggestions.

Pasted image 20250729152900.png

So I've switched the buck converter AND the LDO (though the LDO was a drop in replacement so I only changed the name), and I also fixed up the USB/PSU 5V switching mosfet.

It was pretty boring so I'll just show the final schematic:

Pasted image 20250729152952.png

*I also added no-connect flags to the entire MCU, but no one really care about that*

I then re-assigned all the footprints and went back to the PCB! I did a bunch of organizing components some more, I'll show that in the next day though because there will be more to show.

## Day 8 - Fully Organized PCB - 10 Hours

Now while organizing my PCB, I had to switch a lot of things, notable, every single diode footprint was off and a bunch of resistor sizing's and stuff were wrong too.

It probably took me a solid 2 hours to get all the footprints straight for a second time but it turned out pretty well.

Anyways, I then proceeded to spend a couple hours laying out all the components to be perfectly organized, and I got something very nice!

Pasted image 20250729233321.png

Now this organization took way longer than I thought it would because LOTS of the footprints were off, and and then I had to keep on adding suggestions from people which made me change them more, like switching the buck and the LDO, and it's a never ending back and forth.

Anyways there's still some stuff like the positioning on some of the things aren't right for the diodes that I fixed so I kind of need to fix that stuff.

And after a bit of time and some more review from the guys on the KiCad discord server, I have a PRETTY solid organization:

Pasted image 20250730001939.png

I then compressed all the parts together to get this:

Pasted image 20250730024450.png

I make it seem easy of course, but this is after like 4 rounds of iteration so when I go to route, it's pretty clean!

I posted this on the KiCad discord server and then Salmon (my favorite KiCad elf) pointed out that the NMOS's on the heaters aren't the right footprints! So now I gotta fix those! Also thanks so much to Salmon on the KiCad discord server, probably one of the most helpful people I've met online.

And then after an insanely absurd amount of time, I've gotten to something very nice!

Pasted image 20250730154025.png

Now I just have to orient all the silkscreen so it's nice and organized, and then do the finishing alignments, and it'll be ready to route!

I also forgot, I still need to add some mounting holes, so after adding those, I added the edge to define the PCB, and it's pretty much ready to route!

Pasted image 20250730195133.png

I did a bit more messing around with the organization just to make it a bit cleaner to route, just moving parts basically so rat's are closer to each other.

Now the stackup of my board is going to be as follows: F.Cu, GND, POWER, B.Cu, so I'm going to add the 4 layers onto the board, and then do a power/GND fill:

Pasted image 20250730202943.png

Anyways I'll save the rest of the routing for tomorrow!

## Day 9 - Routing the PCB - 12 Hours

Now I got a lot of stuff to do, I gotta route this entire PCB and I don't have much time left to submit!

First I added all the via's to the ground and power planes to connect the ratlines. I also fixed some intersecting parts which wouldn't work! Way less ratlines now!

Pasted image 20250730234508.png

And then I usually start with the chonky things that take lots of current or voltage, you kind of just want to route these based off current size, voltage and noise levels, and also what's close:

Pasted image 20250731021015.png

Signal pins are small, high current is large, high voltage depends.

And then I improved the power a bit more, and I wired some of the smaller stuff on the board!

Pasted image 20250731025725.png

Mind you, these screenshots are nearly 3 hours apart, this is NOT a short process. I'm also still a beginner, so I need a lot of help from others when designing this, so I'm constantly iterating on it!

And then I got a really good suggestion to move the enstop connectors so that I could fit the SD Card on, so I deleted like half my traces and put it on!

Pasted image 20250731113428.png

Looks WAY better! This is absolutely sick!

After all this, I did all the signal pins from the MCU pretty much, I try to stick to one color going one way, the other color going the other way, and planning the routes out in your head beforehand helps alot!

Pasted image 20250731143619.png

Anyways I finished up all the signal routes, and it looks beautiful! There's not much to say about it, except for it took a LONG time.

Pasted image 20250731193646.png

And now I just have to add the power plane. The VIN power rail will be the largest, followed by the 5V rail which is a bit smaller, and then I can just attach the stuff that kind of needs more and less current like so:

Pasted image 20250731193740.png

The important thing I had to keep in mind during this was the large current of the heater's, and that's one of the reasons I put the VIN so close to them, because they need high current, so I can just do a ground fill there.

Anyways, now I just have to fix all the DRC errors and we'll be good! There were about 30 errors, I fixed all of them up, nothing too crazy, mostly just unconnected things, and this board is BEAUTIFUL.

Pasted image 20250731193850.png

At just 80x90mm this is a powerful, yet small and affordable board, it's beautiful!

Now I'm pretty dead inside and exhausted from making this board, this was shear insanity, but it turned out absolutely amazing!

To anyone reading this, thanks so much to @Fisheiyy on GH for all of his help and the people on reddit for helping me too!

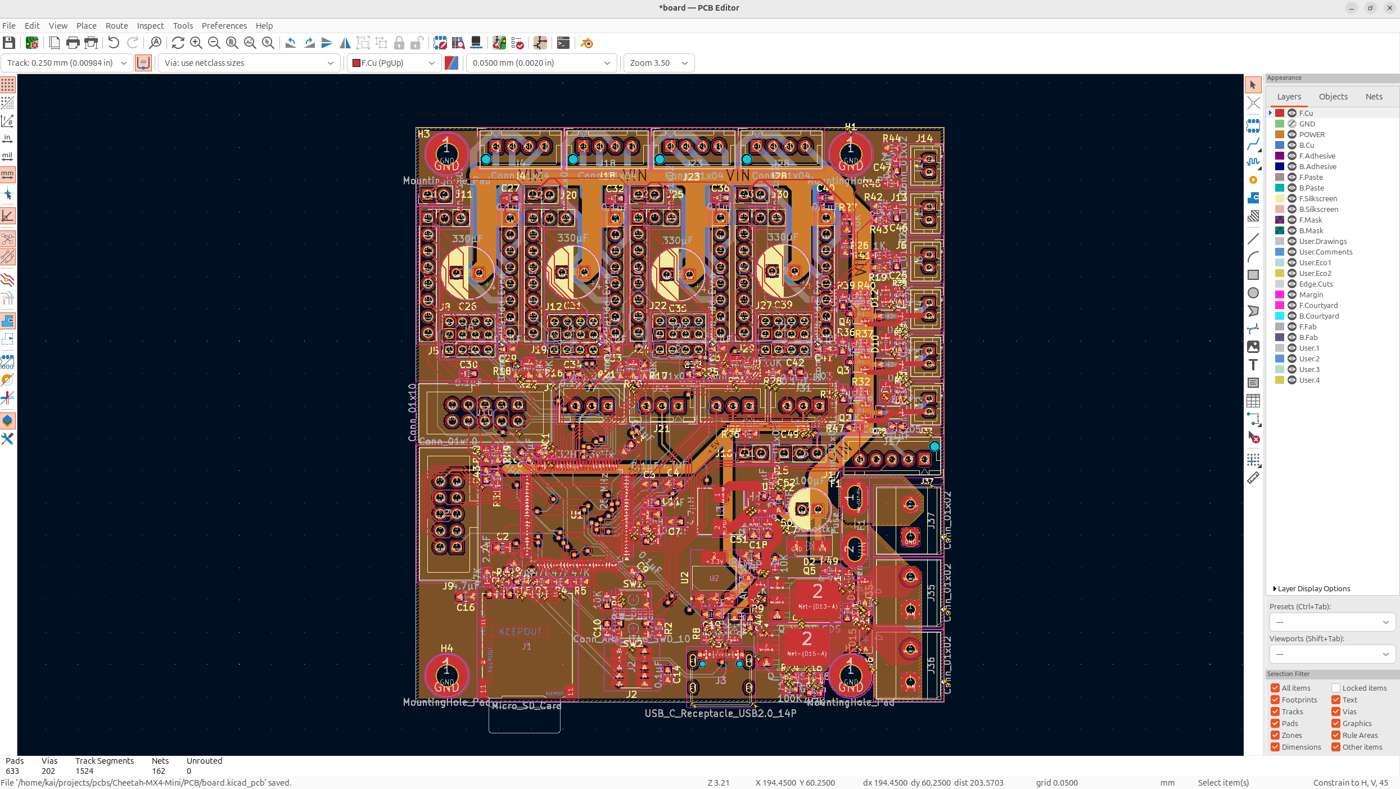
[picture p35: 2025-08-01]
journal/Pasted image 20250731195756.png

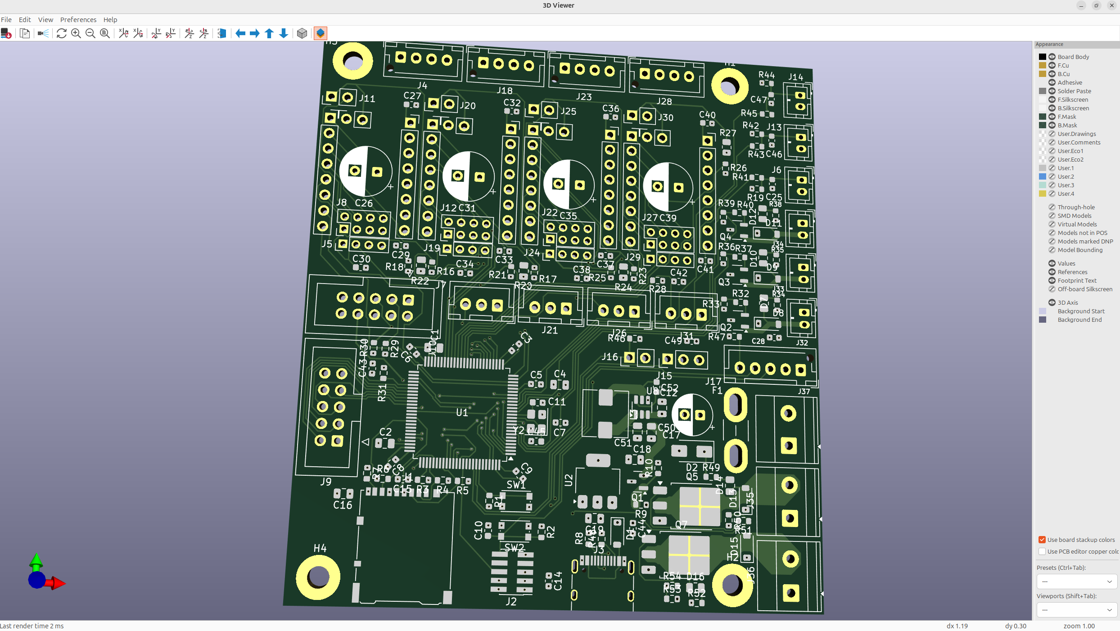
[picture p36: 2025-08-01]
journal/Pasted image 20250731195200.png

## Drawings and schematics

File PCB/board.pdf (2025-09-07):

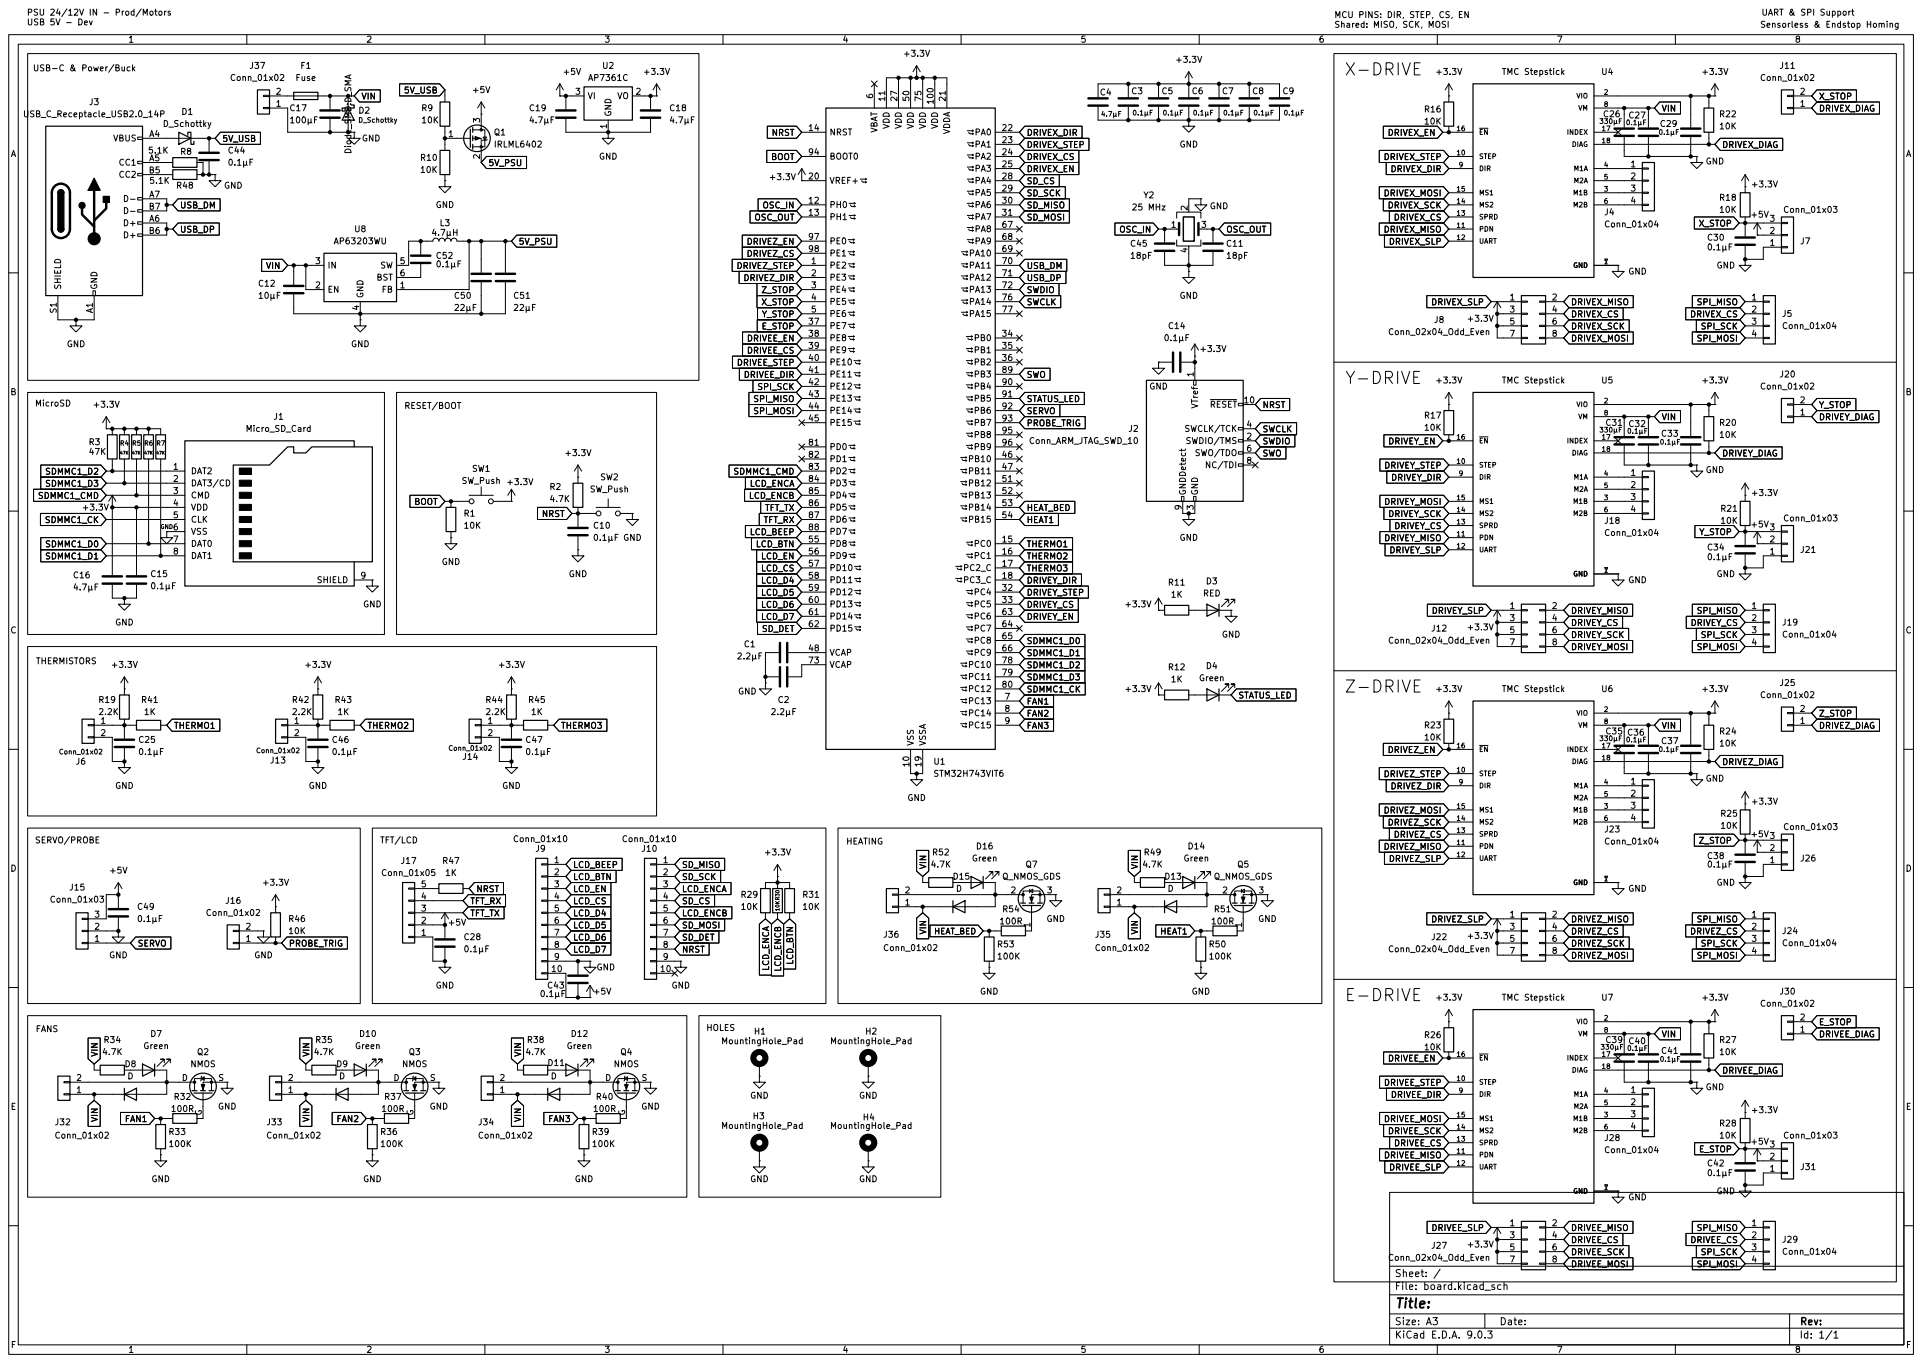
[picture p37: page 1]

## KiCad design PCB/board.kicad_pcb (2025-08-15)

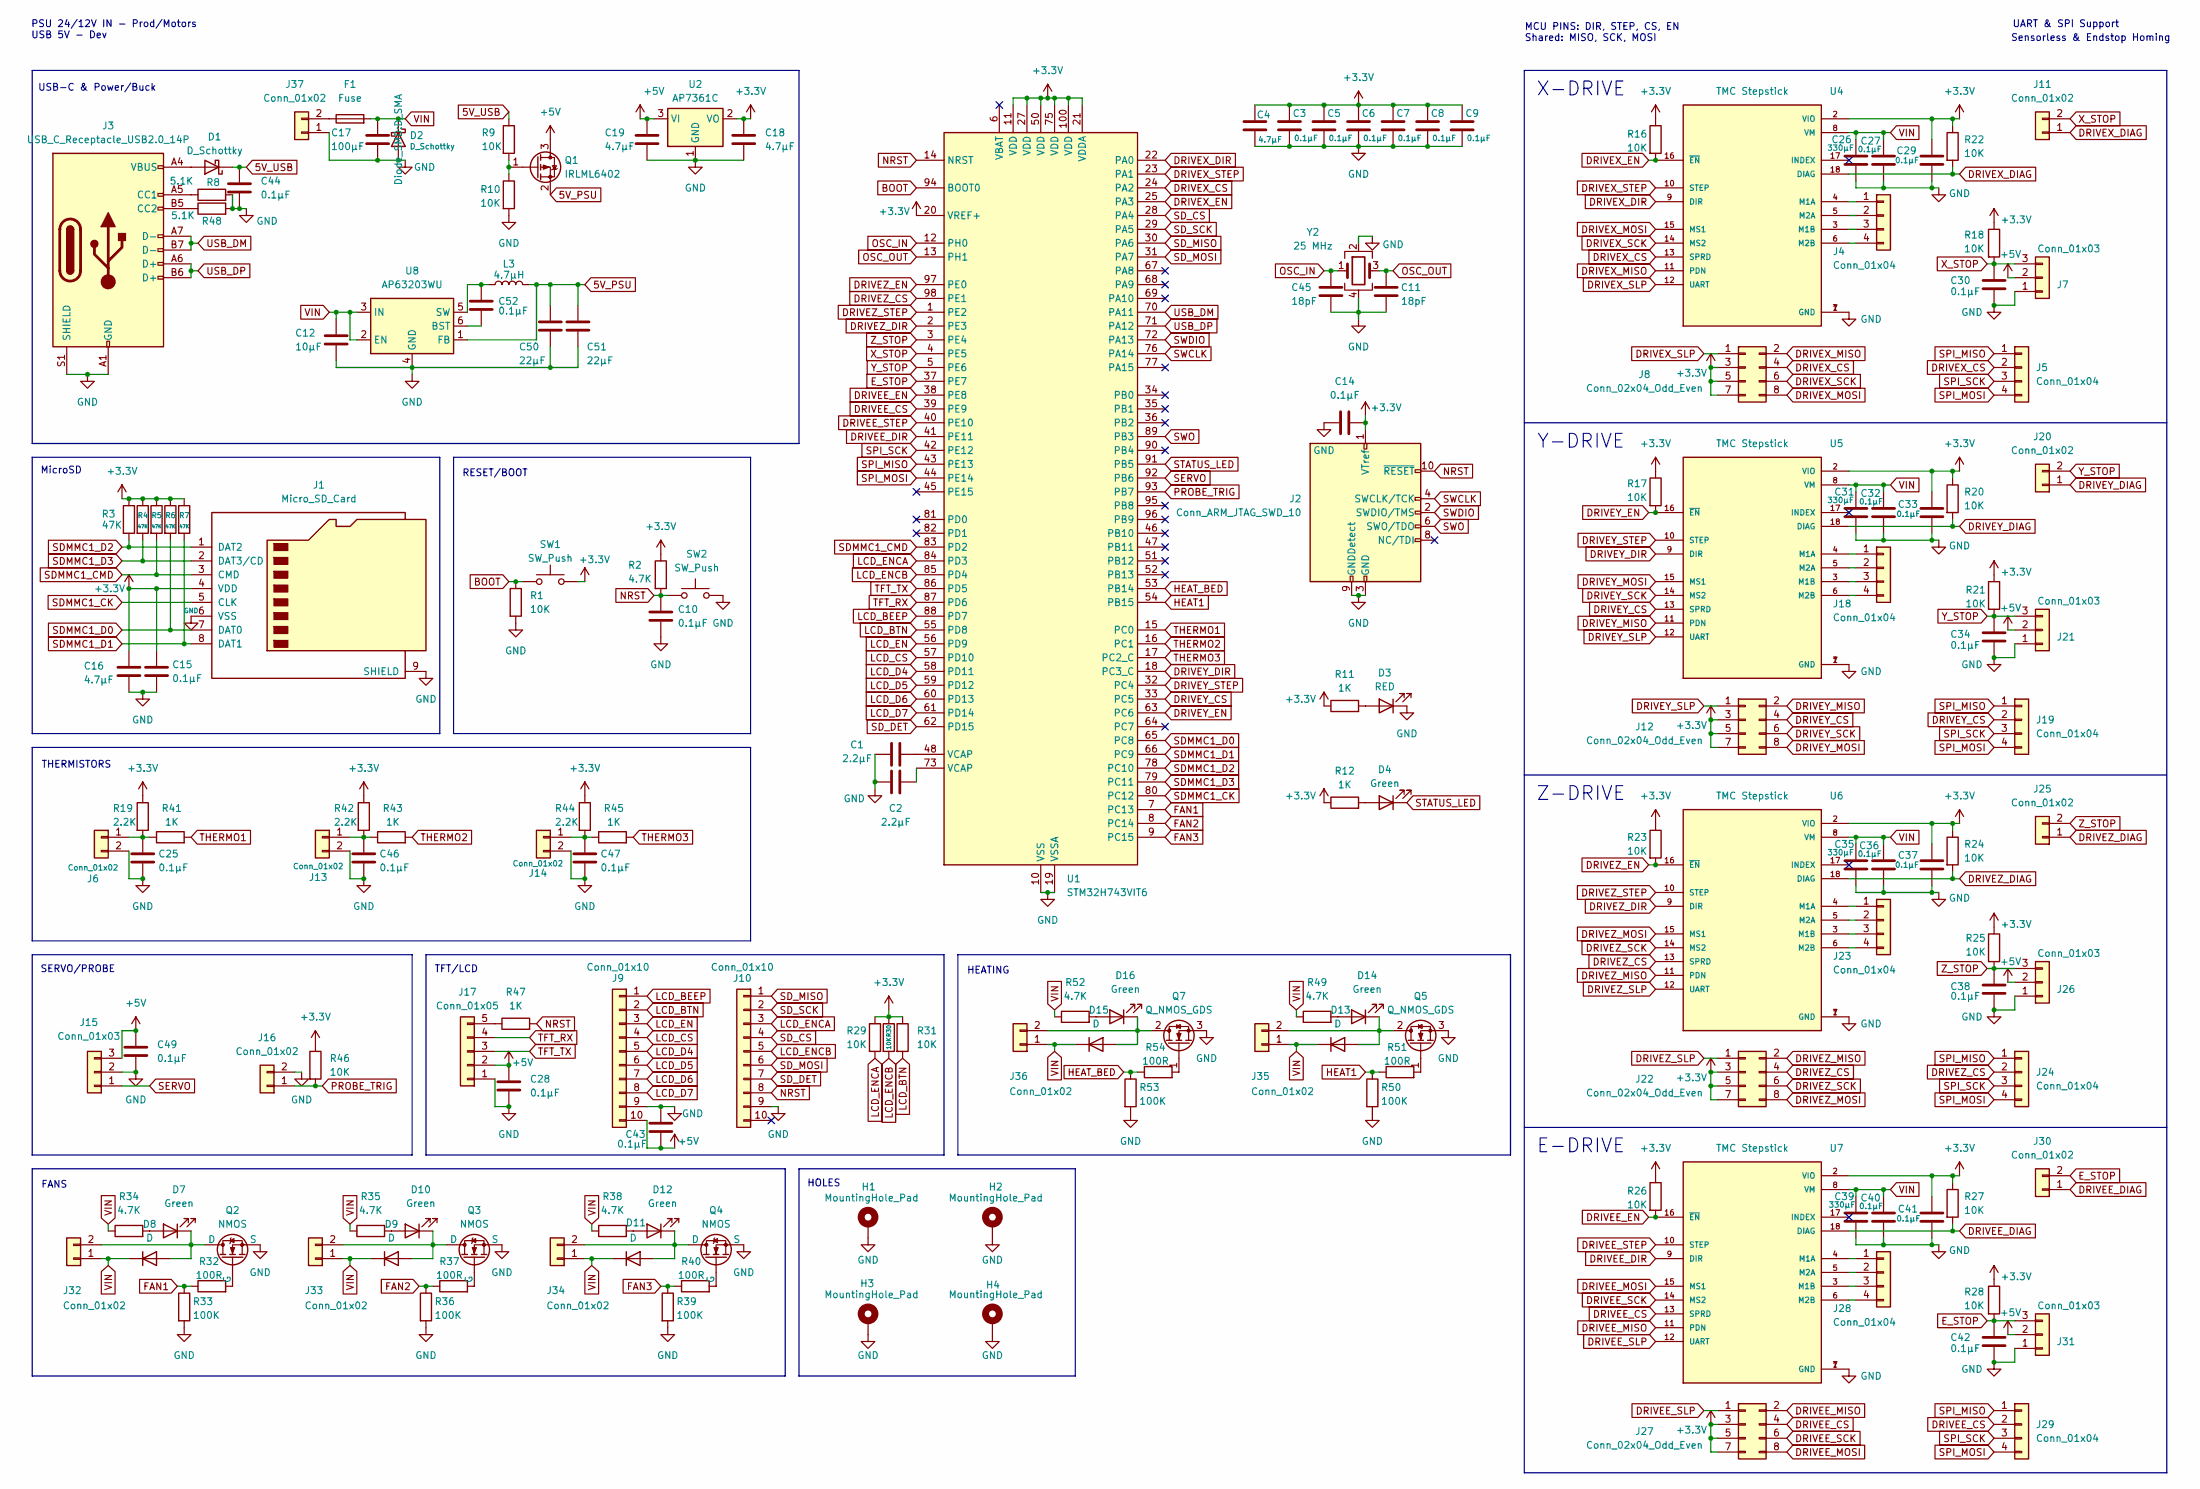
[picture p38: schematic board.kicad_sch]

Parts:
C1, C2: 2.2µF; C_0805_2012Metric
C3, C5, C6, C7, C8, C9, C10, C14, C15, C25, C27, C28, C29, C30, C32, C33, C34, C36, C37, C38, C40, C41, C42, C43, C44, C46, C47, C49, C52: 0.1µF; C_0603_1608Metric
C4, C16, C18, C19: 4.7µF; C_0805_2012Metric
C11, C45: 18pF; C_0603_1608Metric
C12: 10µF; C_0805_2012Metric
C17: 100µF; CP_Radial_D6.3mm_P2.50mm
C26, C31, C35, C39: 330µF; CP_Radial_D8.0mm_P3.50mm
C50, C51: 22µF; C_0805_2012Metric
D1: D_Schottky; D_SOD-123
D2: D_Schottky; D_SMA
D3: RED; LED_0805_2012Metric
D4, D7, D10, D12, D14, D16: Green; LED_0805_2012Metric
D8, D9, D11, D13, D15: D; D_SOD-123
F1: Fuse; Fuse_Blade_Mini_directSolder
H1, H2, H3, H4: MountingHole_Pad; MountingHole_3.2mm_M3_Pad_TopBottom
J1: Micro_SD_Card; microSD_HC_Hirose_DM3AT-SF-PEJM5
J2: Conn_ARM_JTAG_SWD_10; PinHeader_2x05_P1.27mm_Vertical
J3: USB_C_Receptacle_USB2.0_14P; USB_C_Receptacle_HRO_TYPE-C-31-M-12
J4, J18, J23, J28: Conn_01x04; JST_XH_B4B-XH-AM_1x04_P2.50mm_Vertical
J5, J19, J24, J29: Conn_01x04; PinHeader_1x04_P2.00mm_Vertical
J6, J13, J14, J32, J33, J34: Conn_01x02; JST_PH_B2B-PH-K_1x02_P2.00mm_Vertical
J7, J21, J26, J31: Conn_01x03; JST_XH_B3B-XH-A_1x03_P2.50mm_Vertical
J8, J12, J22, J27: Conn_02x04_Odd_Even; PinHeader_2x04_P2.00mm_Vertical
J9, J10: Conn_01x10; IDC-Header_2x05_P2.54mm_Vertical
J11, J16, J20, J25, J30: Conn_01x02; PinHeader_1x02_P2.54mm_Vertical
J15: Conn_01x03; PinHeader_1x03_P2.54mm_Vertical
J17: Conn_01x05; JST_XH_B5B-XH-AM_1x05_P2.50mm_Vertical
J35, J36, J37: Conn_01x02; TerminalBlock_Phoenix_MKDS-1,5-2-5.08_1x02_P5.08mm_Horizont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
L3: 4.7µH; L_Wuerth_HCM-7070
Q1: IRLML6402; SOT-23
Q2, Q3, Q4: NMOS; SOT-23-3
Q5, Q7: Q_NMOS_GDS; TO-252-3_TabPin2
R1, R9, R10, R16, R17, R18, R21, R23, R25, R26, R28, R29, R30, R31, R46: 10K; R_0603_1608Metric
R2, R34, R35, R38, R49, R52: 4.7K; R_0603_1608Metric
R3, R4, R5, R6, R7: 47K; R_0603_1608Metric
R8, R48: 5.1K; R_0603_1608Metric
R11, R12, R41, R43, R45, R47: 1K; R_0603_1608Metric
R19, R42, R44: 2.2K; R_0603_1608Metric
R20, R22, R24, R27: 10K; R_0805_2012Metric
R32, R37, R40, R51, R54: 100R; R_0603_1608Metric
R33, R36, R39, R50, R53: 100K; R_0603_1608Metric
SW1, SW2: SW_Push; SW_Push_1P1T_NO_CK_KMR2
U1: STM32H743VIT6; LQFP-100_14x14mm_P0.5mm
U2: AP7361C; SOT-223-3_TabPin2
U4, U5, U6, U7: TMC Stepstick; PARTREV 1.20
U8: AP63203WU; TSOT-23-6
Y2: 25 MHz; Crystal_SMD_3225-4Pin_3.2x2.5mm

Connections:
5V_PSU: C50.1, C51.1, L3.2, Q1.2 (S), U8.1 (FB)
5V_USB: C44.1, D1.1 (K), R9.1
+3.3V: C3.1, C4.1, C5.1, C6.1, C7.1, C8.1, C9.1, C14.2, C15.1, C16.1, C18.1, C29.1, C33.1, C37.1, C41.1, J1.4 (VDD), J2.1 (VTref), J8.3, J8.5, J8.7, J12.3, J12.5, J12.7, J22.3, J22.5, J22.7, J27.3, J27.5, J27.7, R2.1, R3.1, R4.1, R5.1, R6.1, R7.1, R11.1, R12.1, R16.1, R17.1, R18.1, R19.1, R20.1, R21.1, R22.1, R23.1, R24.1, R25.1, R26.1, R27.1, R28.1, R29.1, R30.1, R31.1, R42.1, R44.1, R46.1, SW1.2, U1.11 (VDD), U1.20 (VREF+), U1.21 (VDDA), U1.27 (VDD), U1.50 (VDD), U1.75 (VDD), U1.100 (VDD), U2.2 (VO), U4.2 (VIO), U5.2 (VIO), U6.2 (VIO), U7.2 (VIO)
+5V: C19.1, C28.1, C43.2, C49.1, J7.2, J9.10, J15.3, J17.2, J21.2, J26.2, J31.2, Q1.3 (D), U2.3 (VI)
BOOT: R1.1, SW1.1, U1.94 (BOOT0)
DRIVEE_CS: J27.4, J29.2, U1.39 (PE9), U7.13 (SPRD)
DRIVEE_DIAG: J30.1, R27.2, U7.18 (DIAG)
DRIVEE_DIR: U1.41 (PE11), U7.9 (DIR)
DRIVEE_EN: R26.2, U1.38 (PE8), U7.16 (~EN)
DRIVEE_MISO: J27.2, U7.11 (PDN)
DRIVEE_MOSI: J27.8, U7.15 (MS1)
DRIVEE_SCK: J27.6, U7.14 (MS2)
DRIVEE_SLP: J27.1, U7.12 (UART)
DRIVEE_STEP: U1.40 (PE10), U7.10 (STEP)
DRIVEX_CS: J5.2, J8.4, U1.24 (PA2), U4.13 (SPRD)
DRIVEX_DIAG: J11.1, R22.2, U4.18 (DIAG)
DRIVEX_DIR: U1.22 (PA0), U4.9 (DIR)
DRIVEX_EN: R16.2, U1.25 (PA3), U4.16 (~EN)
DRIVEX_MISO: J8.2, U4.11 (PDN)
DRIVEX_MOSI: J8.8, U4.15 (MS1)
DRIVEX_SCK: J8.6, U4.14 (MS2)
DRIVEX_SLP: J8.1, U4.12 (UART)
DRIVEX_STEP: U1.23 (PA1), U4.10 (STEP)
DRIVEY_CS: J12.4, J19.2, U1.33 (PC5), U5.13 (SPRD)
DRIVEY_DIAG: J20.1, R20.2, U5.18 (DIAG)
DRIVEY_DIR: U1.18 (PC3_C), U5.9 (DIR)
DRIVEY_EN: R17.2, U1.63 (PC6), U5.16 (~EN)
DRIVEY_MISO: J12.2, U5.11 (PDN)
DRIVEY_MOSI: J12.8, U5.15 (MS1)
DRIVEY_SCK: J12.6, U5.14 (MS2)
DRIVEY_SLP: J12.1, U5.12 (UART)
DRIVEY_STEP: U1.32 (PC4), U5.10 (STEP)
DRIVEZ_CS: J22.4, J24.2, U1.98 (PE1), U6.13 (SPRD)
DRIVEZ_DIAG: J25.1, R24.2, U6.18 (DIAG)
DRIVEZ_DIR: U1.2 (PE3), U6.9 (DIR)
DRIVEZ_EN: R23.2, U1.97 (PE0), U6.16 (~EN)
DRIVEZ_MISO: J22.2, U6.11 (PDN)
DRIVEZ_MOSI: J22.8, U6.15 (MS1)
DRIVEZ_SCK: J22.6, U6.14 (MS2)
DRIVEZ_SLP: J22.1, U6.12 (UART)
DRIVEZ_STEP: U1.1 (PE2), U6.10 (STEP)
E_STOP: C42.1, J30.2, J31.3, R28.2, U1.37 (PE7)
FAN1: R32.1, R33.1, U1.7 (PC13)
FAN2: R36.1, R37.1, U1.8 (PC14)
FAN3: R39.1, R40.1, U1.9 (PC15)
GND: C1.1, C2.1, C3.2, C4.2, C5.2, C6.2, C7.2, C8.2, C9.2, C10.2, C11.1, C12.2, C14.1, C15.2, C16.2, C17.2, C18.2, C19.2, C25.2, C26.2, C27.2, C28.2, C29.2, C30.2, C31.2, C32.2, C33.2, C34.2, C35.2, C36.2, C37.2, C38.2, C39.2, C40.2, C41.2, C42.2, C43.1, C44.2, C45.1, C46.2, C47.2, C49.2, C50.2, C51.2, D2.2 (A), D3.1 (K), H1.1, H2.1, H3.1, H4.1, J1.6 (VSS), J1.9 (SHIELD), J2.3 (GND), J2.5 (GND), J2.9 (GNDDetect), J3.A1 (GND), J3.A12 (GND), J3.B1 (GND), J3.B12 (GND), J3.S1 (SHIELD), J6.2, J7.1, J9.9, J10.9, J13.2, J14.2, J15.2, J16.2, J17.1, J21.1, J26.1, J31.1, J37.1, Q2.3 (S), Q3.3 (S), Q4.3 (S), Q5.3 (S), Q7.3 (S), R1.2, R8.2, R10.2, R33.2, R36.2, R39.2, R48.2, R50.2, R53.2, SW2.2, U1.10 (VSS), U1.19 (VSSA), U1.26 (VSS), U1.49 (VSS), U1.74 (VSS), U1.99 (VSS), U2.1 (GND), U4.1 (GND), U4.7 (GND), U5.1 (GND), U5.7 (GND), U6.1 (GND), U6.7 (GND), U7.1 (GND), U7.7 (GND), U8.4 (GND), Y2.2, Y2.4
HEAT1: R50.1, R51.1, U1.54 (PB15)
HEAT_BED: R53.1, R54.1, U1.53 (PB14)
LCD_BEEP: J9.1, U1.88 (PD7)
LCD_BTN: J9.2, R31.2, U1.55 (PD8)
LCD_CS: J9.4, U1.57 (PD10)
LCD_D4: J9.5, U1.58 (PD11)
LCD_D5: J9.6, U1.59 (PD12)
LCD_D6: J9.7, U1.60 (PD13)
LCD_D7: J9.8, U1.61 (PD14)
LCD_EN: J9.3, U1.56 (PD9)
LCD_ENCA: J10.3, R29.2, U1.84 (PD3)
LCD_ENCB: J10.5, R30.2, U1.85 (PD4)
NRST: C10.1, J2.10 (~RESET), J10.8, R2.2, R47.2, SW2.1, U1.14 (NRST)
unnamed: C1.2, U1.48 (VCAP)
unnamed: C2.2, U1.73 (VCAP)
unnamed: D1.2 (A), J3.A4 (VBUS), J3.A9 (VBUS), J3.B4 (VBUS), J3.B9 (VBUS)
unnamed: D3.2 (A), R11.2
unnamed: D4.2 (A), R12.2
unnamed: D7.2 (A), R34.2
unnamed: D7.1 (K), D8.2 (A), J32.2, Q2.1 (D)
unnamed: D10.2 (A), R35.2
unnamed: D9.2 (A), D10.1 (K), J33.2, Q3.1 (D)
unnamed: D11.2 (A), D12.1 (K), J34.2, Q4.1 (D)
unnamed: D12.2 (A), R38.2
unnamed: D13.2 (A), D14.1 (K), J35.2, Q5.2 (D)
unnamed: D14.2 (A), R49.2
unnamed: D15.2 (A), D16.1 (K), J36.2, Q7.2 (D)
unnamed: D16.2 (A), R52.2
unnamed: J3.A5 (CC1), R8.1
unnamed: J3.B5 (CC2), R48.1
unnamed: J4.1, U4.4 (M1A)
unnamed: J4.2, U4.5 (M2A)
unnamed: J4.3, U4.3 (M1B)
unnamed: J4.4, U4.6 (M2B)
unnamed: C25.1, J6.1, R19.2, R41.1
unnamed: C46.1, J13.1, R42.2, R43.1
unnamed: C47.1, J14.1, R44.2, R45.1
unnamed: J17.5, R47.1
unnamed: J18.1, U5.4 (M1A)
unnamed: J18.2, U5.5 (M2A)
unnamed: J18.3, U5.3 (M1B)
unnamed: J18.4, U5.6 (M2B)
unnamed: J23.1, U6.4 (M1A)
unnamed: J23.2, U6.5 (M2A)
unnamed: J23.3, U6.3 (M1B)
unnamed: J23.4, U6.6 (M2B)
unnamed: J28.1, U7.4 (M1A)
unnamed: J28.2, U7.5 (M2A)
unnamed: J28.3, U7.3 (M1B)
unnamed: J28.4, U7.6 (M2B)
unnamed: F1.1, J37.2
unnamed: Q1.1 (G), R9.2, R10.1
unnamed: Q2.2 (G), R32.2
unnamed: Q3.2 (G), R37.2
unnamed: Q4.2 (G), R40.2
unnamed: Q5.1 (G), R51.2
unnamed: Q7.1 (G), R54.2
unnamed: C52.2, U8.6 (BST)
unnamed: C52.1, L3.1, U8.5 (SW)
OSC_IN: C45.2, U1.12 (PH0), Y2.1
OSC_OUT: C11.2, U1.13 (PH1), Y2.3
PROBE_TRIG: J16.1, R46.2, U1.93 (PB7)
SDMMC1_CK: J1.5 (CLK), U1.80 (PC12)
SDMMC1_CMD: J1.3 (CMD), R5.2, U1.83 (PD2)
SDMMC1_D0: J1.7 (DAT0), R6.2, U1.65 (PC8)
SDMMC1_D1: J1.8 (DAT1), R7.2, U1.66 (PC9)
SDMMC1_D2: J1.1 (DAT2), R3.2, U1.78 (PC10)
SDMMC1_D3: J1.2 (DAT3/CD), R4.2, U1.79 (PC11)
SD_CS: J10.4, U1.28 (PA4)
SD_DET: J10.7, U1.62 (PD15)
SD_MISO: J10.1, U1.30 (PA6)
SD_MOSI: J10.6, U1.31 (PA7)
SD_SCK: J10.2, U1.29 (PA5)
SERVO: J15.1, U1.92 (PB6)
SPI_MISO: J5.1, J19.1, J24.1, J29.1, U1.43 (PE13)
SPI_MOSI: J5.4, J19.4, J24.4, J29.4, U1.44 (PE14)
SPI_SCK: J5.3, J19.3, J24.3, J29.3, U1.42 (PE12)
STATUS_LED: D4.1 (K), U1.91 (PB5)
SWCLK: J2.4 (SWCLK/TCK), U1.76 (PA14)
SWDIO: J2.2 (SWDIO/TMS), U1.72 (PA13)
SWO: J2.6 (SWO/TDO), U1.89 (PB3)
TFT_RX: J17.4, U1.87 (PD6)
TFT_TX: J17.3, U1.86 (PD5)
THERMO1: R41.2, U1.15 (PC0)
THERMO2: R43.2, U1.16 (PC1)
THERMO3: R45.2, U1.17 (PC2_C)
USB_DM: J3.A7 (D-), J3.B7 (D-), U1.70 (PA11)
USB_DP: J3.A6 (D+), J3.B6 (D+), U1.71 (PA12)
VIN: C12.1, C17.1, C26.1, C27.1, C31.1, C32.1, C35.1, C36.1, C39.1, C40.1, D2.1 (K), D8.1 (K), D9.1 (K), D11.1 (K), D13.1 (K), D15.1 (K), F1.2, J32.1, J33.1, J34.1, J35.1, J36.1, R34.1, R35.1, R38.1, R49.1, R52.1, U4.8 (VM), U5.8 (VM), U6.8 (VM), U7.8 (VM), U8.2 (EN), U8.3 (IN)
X_STOP: C30.1, J7.3, J11.2, R18.2, U1.4 (PE5)
Y_STOP: C34.1, J20.2, J21.3, R21.2, U1.5 (PE6)
Z_STOP: C38.1, J25.2, J26.3, R25.2, U1.3 (PE4)

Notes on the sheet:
PSU 24/12V IN - Prod/Motors USB 5V - Dev
MicroSD
Y-DRIVE
UART & SPI Support
SERVO/PROBE
HOLES
Z-DRIVE
THERMISTORS
USB-C & Power/Buck
X-DRIVE
TFT/LCD
MCU PINS: DIR, STEP, CS, EN Shared: MISO, SCK, MOSI
HEATING
E-DRIVE
Sensorless & Endstop Homing
FANS
RESET/BOOT

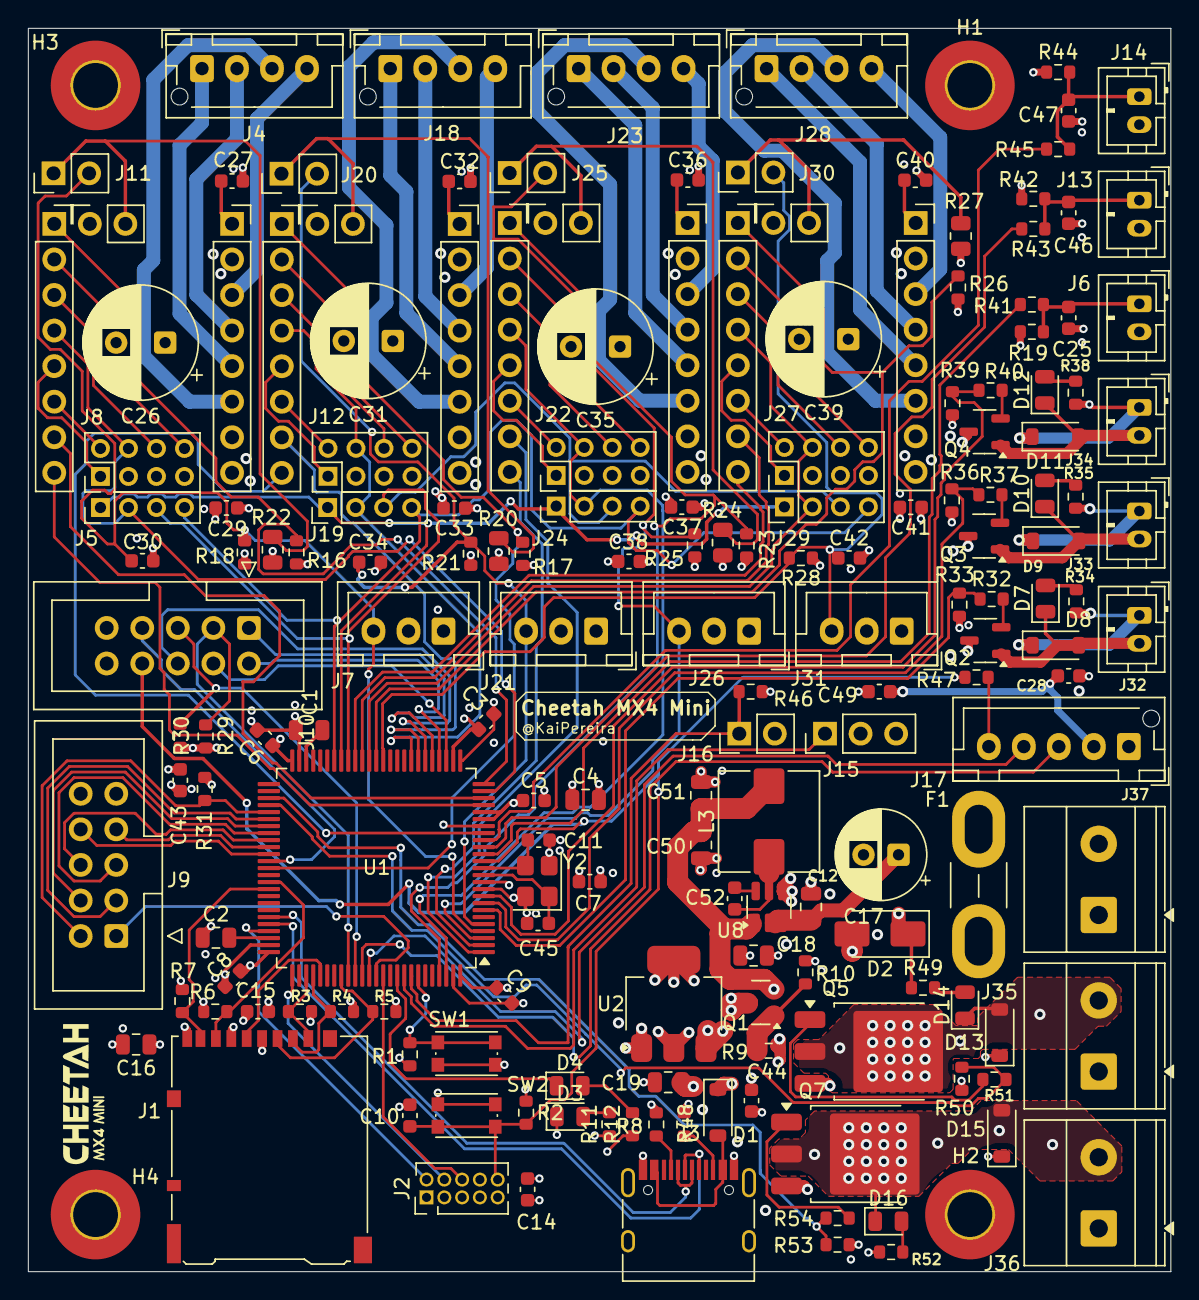
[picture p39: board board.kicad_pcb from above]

Board: 4 copper layers, 81.6 x 88.8 mm, 169 parts (0 on the bottom side), 138 nets.

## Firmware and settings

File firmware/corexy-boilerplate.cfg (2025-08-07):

# This file is an example config file for corexy (and also h-bot)
# style printers. One may copy and edit this file to configure a new
# corexy printer.

# DO NOT COPY THIS FILE WITHOUT CAREFULLY READING AND UPDATING IT
# FIRST. Incorrectly configured parameters may cause damage.

# See docs/Config_Reference.md for a description of parameters.

[stepper_x]
step_pin: PF0
dir_pin: PF1
enable_pin: !PD7
microsteps: 16
rotation_distance: 40
endstop_pin: ^PE5
position_endstop: 0
position_max: 200
homing_speed: 50

[stepper_y]
step_pin: PF6
dir_pin: PF7
enable_pin: !PF2
microsteps: 16
rotation_distance: 40
endstop_pin: ^PJ1
position_endstop: 0
position_max: 200
homing_speed: 50

[stepper_z]
step_pin: PL3
dir_pin: PL1
enable_pin: !PK0
microsteps: 16
rotation_distance: 8
endstop_pin: ^PD3
position_endstop: 0.5
position_max: 200

[extruder]
step_pin: PA4
dir_pin: PA6
enable_pin: !PA2
microsteps: 16
rotation_distance: 33.500
nozzle_diameter: 0.400
filament_diameter: 1.750
heater_pin: PB4
sensor_type: ATC Semitec 104GT-2
sensor_pin: PK5
control: pid
pid_Kp: 22.2
pid_Ki: 1.08
pid_Kd: 114
min_temp: 0
max_temp: 250

[heater_bed]
heater_pin: PH5
sensor_type: EPCOS 100K B57560G104F
sensor_pin: PK6
control: watermark
min_temp: 0
max_temp: 130

[fan]
pin: PH6

[mcu]
serial: /dev/ttyACM0

[printer]
kinematics: corexy
max_velocity: 300
max_accel: 3000
max_z_velocity: 25
max_z_accel: 30

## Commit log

2025-07-20 started project, this is probably a bad idea lol
    [3D-Printer-Driver-Board.kicad_pcb, 3D-Printer-Driver-Board.kicad_sch]
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2025-07-21 started the schematic, I still think this is a horrible idea, but it's going to be so cool
    [board.kicad_sch]
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2025-07-21 adding boot and fixed the decoupling
    [board.kicad_sch]
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2025-07-21 separate the boot/reset schematic into a little box!
    [board.kicad_sch]
2025-07-21 added crystal oscillator
    [board.kicad_sch]
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2025-07-21 adding my SWD debugger headers, I think I'm using the wrong symbol though
    [board.kicad_sch]
2025-07-22 added the JTAG/SWD connector, and made it more detailed
    [board.kicad_sch]
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2025-07-22 connected shield to GND and updated journal with SD card
    [board.kicad_sch]
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2025-07-23 some buck converter stuff, I think I need to use an LDO instead because it was suggested, also changed the fuse to a polyfuse
    [board.kicad_sch]
2025-07-23 added the new buck converter but the schematic looks a tad messy and the value's aren't in eyt
    [board.kicad_sch]
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2025-07-24 P-Mosfet for PSU/USB switching and added the LDO
    [board.kicad_sch]
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2025-07-24 added a new TMC symbol from snapeda
    [board.kicad_sch]
2025-07-24 added stepstick driver, I think it's fine, but I'm not too sure
    [board.kicad_sch]
2025-07-24 re-organized the schematic and bit more and did the journal for the stepper
    [board.kicad_sch]
2025-07-24 added the endstop, but now I have to implement both sensorless and endstop home
    [board.kicad_sch]
2025-07-24 added endstop connectors and started working on footprints and stuff which was dumb not to do initially, also already added the journal log
    [board.kicad_sch]
2025-07-24 fixing the TMC2209 stepstick, I was wiring it like the IC, not the module for some reason and it was a bit off in general
    [board.kicad_sch]
2025-07-24 added decoupling caps to power pins on drivers
    [board.kicad_sch]
2025-07-24 added some thermistor stuff and re-organized a bit
    [board.kicad_sch]
2025-07-25 fixed the UART on the drivers
    [board.kicad_sch]
2025-07-25 sd card peripheral was messed up for some reason
    [board.kicad_sch]
2025-07-25 added all motor drivers in (x, y, z, e0)
    [board.kicad_sch]
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2025-07-25 fixed usb cc pin not pulled down and lower bulk capacitance cap on the PSU
    [board.kicad_sch]
2025-07-25 fixing capacitors on the motor drivers, removed the other drivers while making edits
    [board.kicad_sch]
2025-07-25 fixed pullups on thermistors
    [board.kicad_sch]
2025-07-26 finally fixed the UART on my drivers! Thanks salmon :D
    [board.kicad_sch]
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2025-07-26 working on more SPI stuff, working on jumpers
    [board.kicad_sch]
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2025-07-26 I might crash out from SPI but this MIGHT be fine?
    [board.kicad_sch]
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2025-07-26 added all the drivers, but haven't named them yet
    [board.kicad_sch]
2025-07-26 kind of going insane, but I can't figure out how UART is getting a signal??
    [board.kicad_sch]
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2025-07-27 adding TFT to journal and fixing it up on the schematic
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2025-07-27 wired up some more stuff for the LCD's
    [board.kicad_sch]
2025-07-27 re-doing some driver pins because I keep on messing them up
    [board.kicad_sch]
2025-07-27 adding the endstop jumper to switch between sensorless and endstop
    [board.kicad_sch]
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2025-07-27 finished adding all the labels to the actual drivers, just have to put them on the MCU
    [board.kicad_sch]
2025-07-27 some more formatting, almost done adding all the io's for the drivers
    [board.kicad_sch]
2025-07-27 that might be all the labels in the right spots for the drivers?
    [board.kicad_sch]
2025-07-27 updated the journal with all the stuff I did
    [board.kicad_sch]
2025-07-27 some more journaling stuff and pullups on LCD
    [board.kicad_sch]
2025-07-27 updated the journal and added some decoupling to LCD's
    [board.kicad_sch]
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2025-07-28 more footpritns, I should've done this while making the schematic...
    [board.kicad_sch]
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2025-07-28 ALL the footprints except for the TMC stepsticks
    [board.kicad_sch]
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2025-07-28 fixing the footprint for the motor drivers
    [board.kicad_sch]
2025-07-28 fixed all the connectors except the LCD/TFT ones
    [board.kicad_sch]
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2025-07-29 cleaner up some stuff, this would be a good commit to revert too
    [board.kicad_sch]
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2025-07-29 currently aligning all the parts for the pcb
    [board.kicad_pcb]
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2025-07-29 boot/reset and power organization
    [board.kicad_pcb]
2025-07-29 everything organized on the board together, now I just have to precisely put it on, but I gotta figure out the screens first
    [board.kicad_pcb]
2025-07-29 updated sd card, at least I think that was the change?
    [board.kicad_sch]
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2025-07-29 switched symbol to receptacle instead of plug for usb-c
    [board.kicad_pcb, board.kicad_sch]
2025-07-29 actually fixed the usb this time
    [board.kicad_pcb, board.kicad_sch]
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2025-07-29 fixed the crystal pins
    [board.kicad_pcb, board.kicad_sch]
2025-07-29 fixed up the mcu footprint some more
    [board.kicad_pcb]
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2025-07-29 fixing the connector size on the UART/SPI toggle
    [board.kicad_pcb, board.kicad_sch]
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2025-07-29 fixed the buck converter
    [board.kicad_sch]
2025-07-29 new LDO and fixed decoup
    [board.kicad_sch]
2025-07-29 don't go to this commit, can't figure out 5V mosfet switching?
    [board.kicad_pcb, board.kicad_sch]
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2025-07-30 re-oriented, this is a good version to go to
    [board.kicad_pcb]
2025-07-30 starting to compress everything now, motor drivers and mcu down
    [board.kicad_pcb]
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2025-07-30 compressing even more stuff, specifically the power stuff
    [board.kicad_pcb]
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2025-07-30 updated journal, but I need to fix the NMOS on the heaters
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2025-07-30 everything is on nicely, but I may or may not have forgotten mounting holes
    [board.kicad_pcb]
2025-07-30 the board is almost ready to route! Good place to backup too
    [board.kicad_pcb]
2025-07-30 fixed the mosfets on the heaters
    [board.kicad_pcb, board.kicad_sch]
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2025-07-31 lots of powers and gnd's via'd too, I don't really know how to say it lol
    [board.kicad_pcb]
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2025-07-31 routed a display and more stuff on the drivers + journal
    [board.kicad_pcb]
2025-07-31 removing redundant stuff in the schematic and some more routing
    [board.kicad_pcb, board.kicad_sch]
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2025-07-31 hopping off for the night, very good progress though!
    [board.kicad_pcb]
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2025-07-31 wiring the drivers and the mcu some more
    [board.kicad_pcb]
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2025-08-01 only 9 drc errors left!
    [board.kicad_pcb]
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2025-08-01 only 2 drc errors left!
    [board.kicad_pcb]
2025-08-01 finished the PCB (well no drc errors
    [board.kicad_pcb]
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2025-08-01 added footprint BOM to the root directory, will update with a more detailed BOM soon
    [BOM.csv]
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2025-08-01 FMAKING THE INDUCTOR ROUTING BETTER, not adding prod files yet tho, cuz tenting first
    [board.kicad_pcb]
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2025-08-01 fixing 3D models
    [board.kicad_pcb]
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2025-08-03 no more via's on pads (except on mosfets) and re-did mosfet fills for both layers
    [board.kicad_pcb]
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2025-08-05 fixing the BOM
    [board.csv]
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2025-08-06 fixing pcb drc errors
    [board.kicad_pcb]
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2025-08-11 I may be on vacation, but I'm getting this PCB done and dusted!
    [board.kicad_pcb, board.kicad_sch]
2025-08-11 fixing some of the cap placements
    [board.kicad_pcb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]
2025-08-11 update repo for PCBA, for some reason I had corrupt git files
    [board.kicad_pcb, board.kicad_sch]
2025-08-11 fixing usb c
    [board.kicad_pcb, board.kicad_sch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]
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
